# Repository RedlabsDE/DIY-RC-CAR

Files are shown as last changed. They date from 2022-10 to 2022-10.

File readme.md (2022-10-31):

# Create a simple DIY remote controlled car

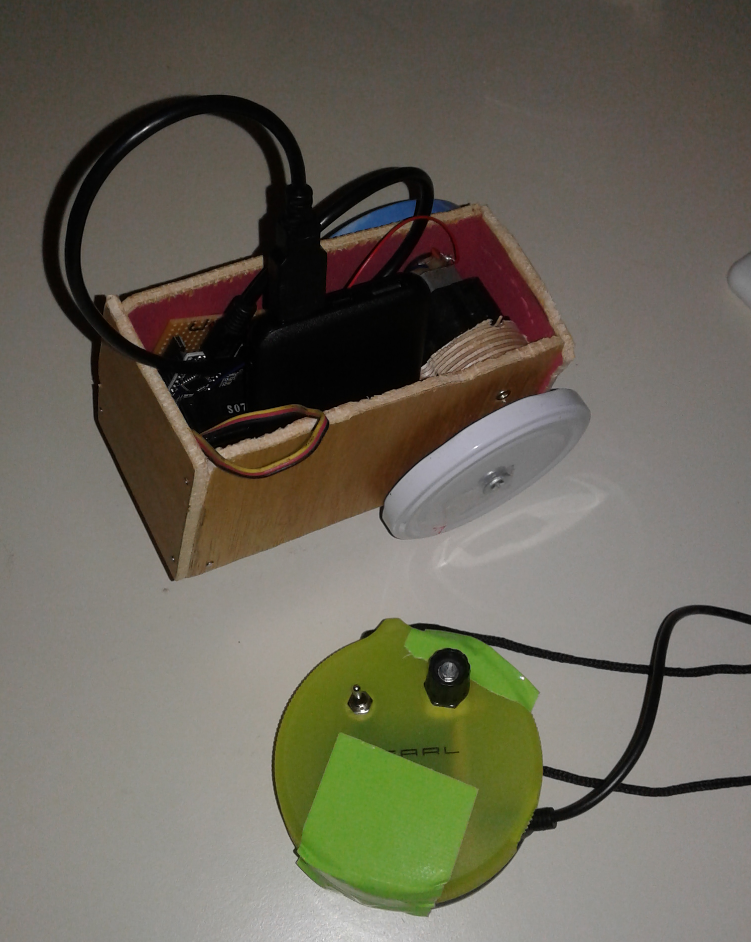
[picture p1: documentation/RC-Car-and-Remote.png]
Car and Remote


### What is this repository for? ###

* Quick summary  
	- RC and Car are bothed based on an arduino and will communicate via a wireless module (NRF24L01, 2.4GHz)
	- The RC (transmitter) looks for user input (Buttons,..) and send current state
	- The Car (receiver) reacts to received user input and set direction and speed of motor
	- Receiver and Transmitter are powered by a small USB Powerbank

## Firmware Setup ##
Too keep it simple, RC (transmitter) and the car (receiver) share the same arduino code.

- upload sketch to transmitter & receicer
```
#define TARGET_TRANSMITTER  1 //Remote Control
#define TARGET_RECEIVER     2 //Car

#define USED_TARGET TARGET_TRANSMITTER //<<< set target to be compiled
```
- check connection: if status LED flashes fast on receiver/transmitter there is no connection (motor stops if connection is lost)

## Hardware Setup ##

- Find schematics of transmitter and receiver in `...\RC-Transceiver\hardware\schematic`
- Find datasheets of used components in `...\RC-Transceiver\hardware\datasheet`

- `NRF24L01:` Transmitter and Receiver use same NRF pin setup. Find nice introduction here:  https://lastminuteengineers.com/nrf24l01-arduino-wireless-communication/

| Signal | Arduino Pin |
|---|---|
| NRF_MOSI 		| 11 |
| NRF_MISO | 12 	|
| NRF_MISO | 13 	|
| NRF_CE 	| 7 	|
| NRF_CSN 	| 8 	|
| NRF_IRQ 	| N/A 	|

### Transmitter ###
- `Board:` Arduino nano (with USB-mini connector)
- `Supply:` 5V (USB Powerbank) via Arduino USB connector
- `NRF24L01:` Connect NRF supply pin to 3V, Arduino Pro Mini: "VCC"
- `Push Buttons:` connect other pin to ground (active low)
- `Status LED:` connect other pin to ground (active high)
- `Potentiometer:` connect upper pin to VCC, lower pin to gnd, add capacitor to gnd on middle pin

| Signal 	| Arduino Pin |
|---		|---		|
| LED_STATUS		|10 		|
| Pushbutton_1 		|2 			|
| Pushbutton_2 		|3 			|
| Poti_1			|0 (A0)			|

### Receiver ###
- `Board:` Arduino nano (with USB-mini connector)
- `Supply:` 5V (USB Powerbank) via Arduino USB connector
- `NRF24L01:` Connect NRF supply pin to 3V, Arduino Nano: "3V3"
- `Status LED:` connect other pin to ground (active high)
- `Servo:` connect supply pin to 5V
- `Motor Driver:` connect supply pin to 5V *(H-Bridge IC could be replaced by 2xNFET + 2xPFET)*
- `DC Motor:` Connect Motor pins to motor driver

| Signal | Arduino Pin |
|---	|---		|
| LED_STATUS	|10 		|
| Servo1_Control|9 			|

| Signal 		| H-Bridge 	| Arduino Pin |
|---		|---	|---	|
| DCM1_GateP_neg	|G4			|3 			|
| DCM1_GateP_pos	|G1			|4 			|
| DCM1_GateN_neg	|G3			|5 (PWM) 		|
| DCM1_GateN_pos	|G2			|6 (PWM) 		|

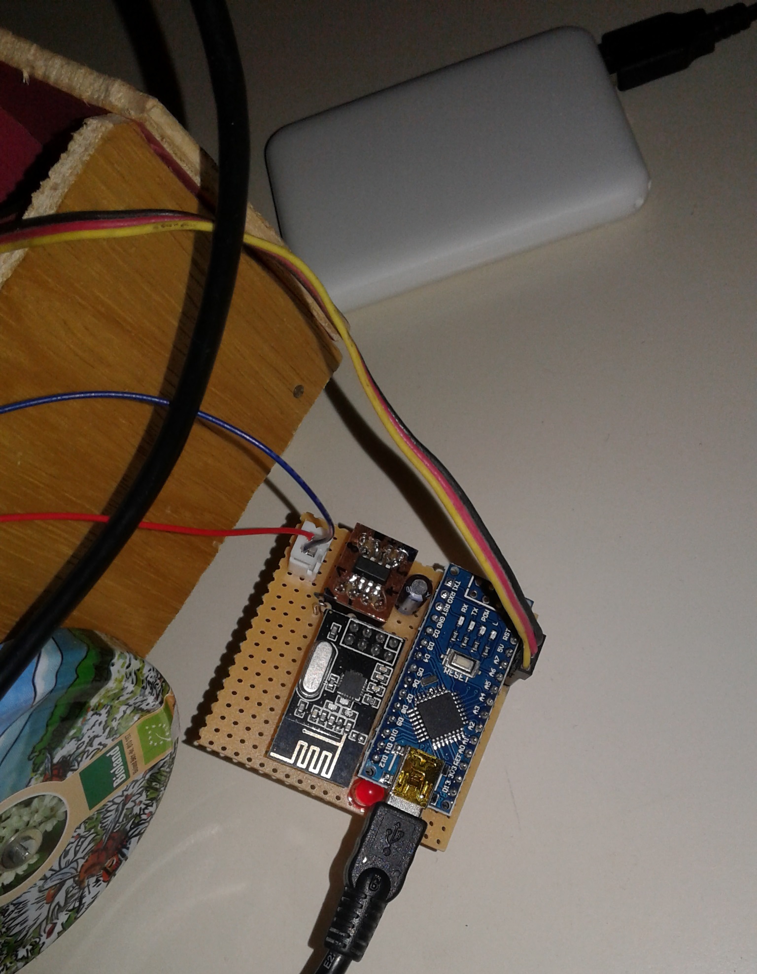
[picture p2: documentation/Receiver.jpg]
Receiver Circuit


## Mechanic Setup ##
### Transmitter ###
- A simple plastic box is used as RC housing
- Set direction of car: use potentiometer
- Move forward/backward: Use dual push switch (push&hold), idle position is stop

### Receiver ###
- As a car frame, wooden plates are nailed together (could be easily done by kids)
- As back wheels old metal caps are screwed to the axis (axis made of threaded standoff)
- Drive car forward and backward: Use single DC Motor to drive both back wheels (old DC motor with gears)
- Set direction of car: Use Servo to set angle of single front wheel (wheel is glued to the servo)

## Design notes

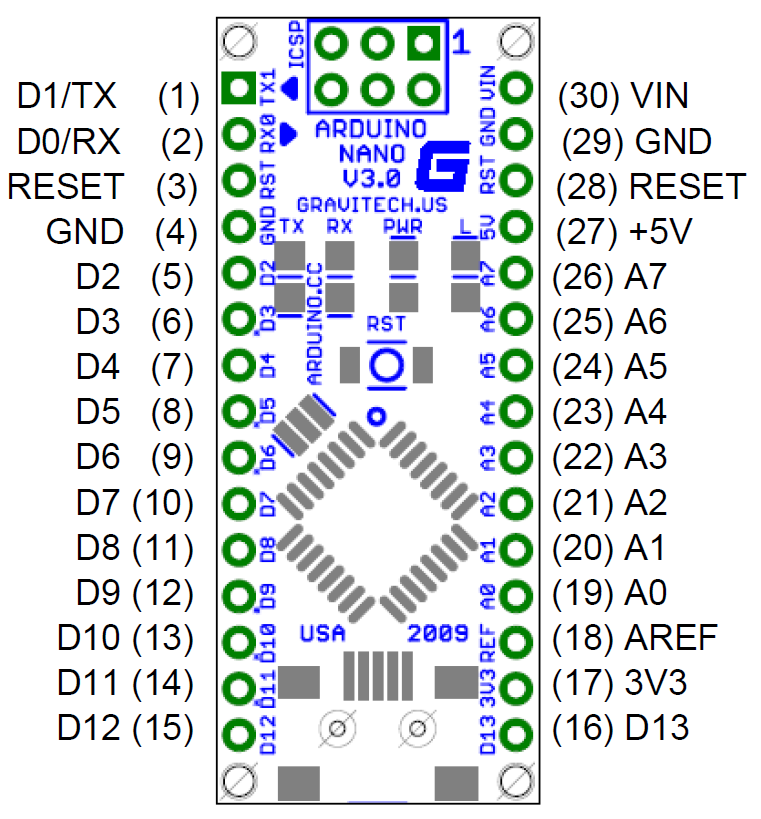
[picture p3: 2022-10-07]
hardware/datasheet/Arduino_Nano_Pinout.png

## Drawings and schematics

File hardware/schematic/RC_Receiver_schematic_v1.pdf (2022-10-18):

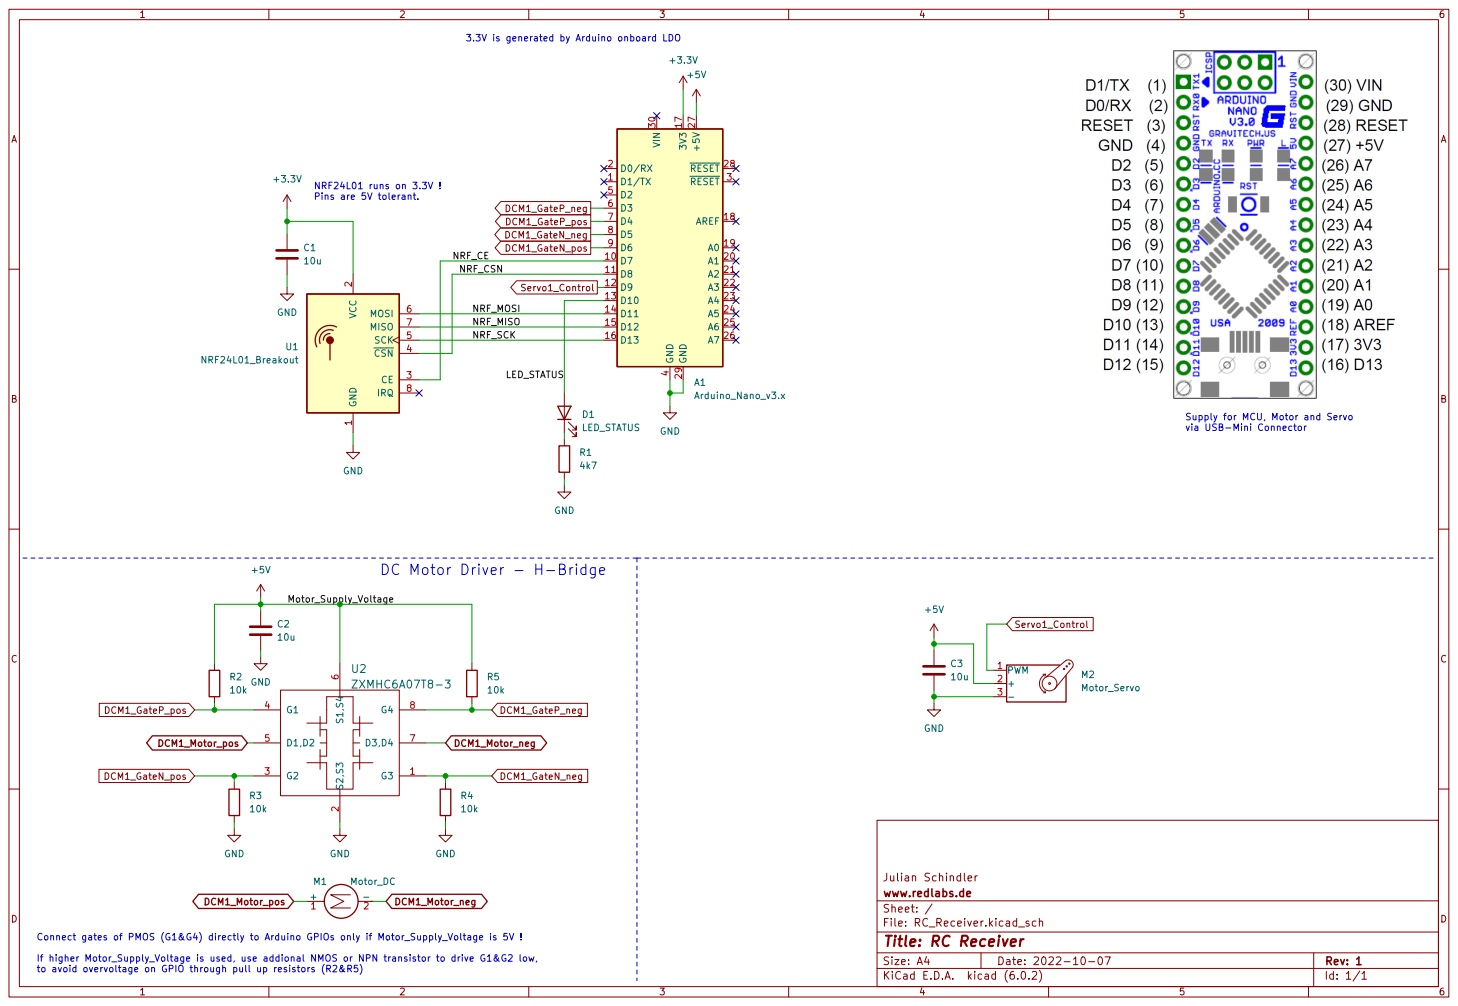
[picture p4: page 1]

2 CE 3 ~{CSN} 4 SCK 5 MOSI 6 MISO 7

Supply for MCU, Motor and Servo

DC Motor Driver - H-Bridge

File: RC_Receiver.kicad_sch Sheet: / www.redlabs.de

Connect gates of PMOS (G1&G4) directly to Arduino GPIOs only if Motor_Supply_Voltage is 5V !

Id: 1/1 Title: RC Receiver

If higher Motor_Supply_Voltage is used, use addional NMOS or NPN transistor to drive G1&G2 low,
to avoid overvoltage on GPIO through pull up resistors (R2&R5)

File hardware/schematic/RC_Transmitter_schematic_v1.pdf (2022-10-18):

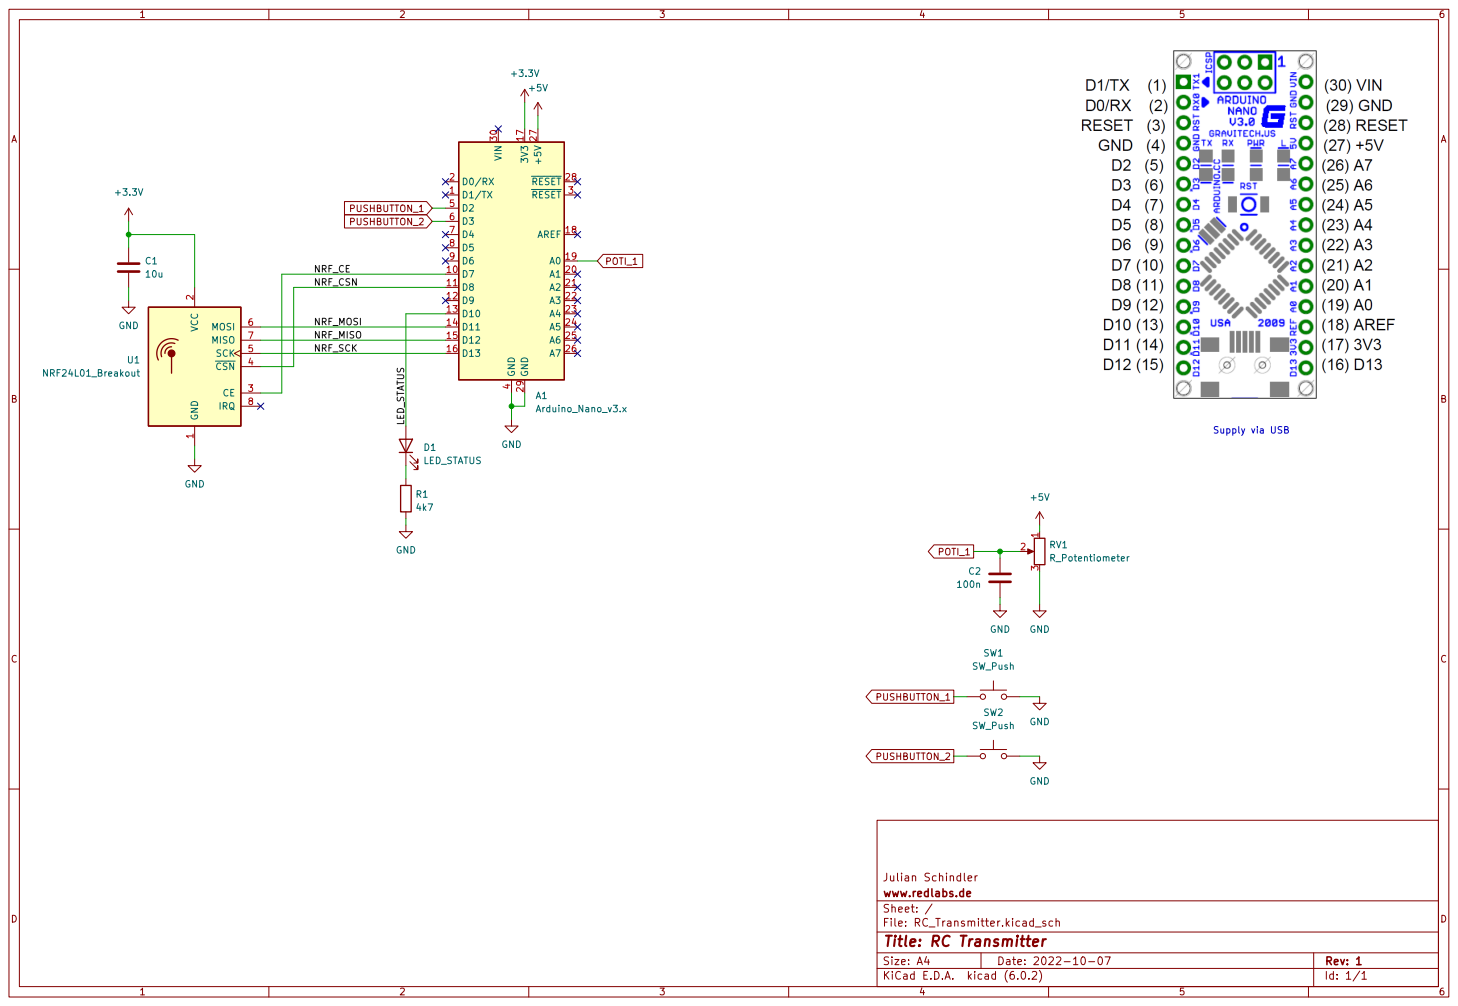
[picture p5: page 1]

2 CE 3 ~{CSN} 4 SCK 5 MOSI 6 MISO 7

File: RC_Transmitter.kicad_sch Sheet: / www.redlabs.de

Id: 1/1 Title: RC Transmitter

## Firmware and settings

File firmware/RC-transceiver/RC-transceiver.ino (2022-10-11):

//////////////////////////////////////////////////////////////////////////////
///
/// \file       RC-transceiver
/// \brief      Remote Control Transmitter and Receiver
/// \author     Julian Schindler
/// \date       21.09.2022
/// \version    1.0
/// \par        Editor
///             Arduino IDE
/// \par        Board
///             Arduino Pro or Pro Mini
/// \par        Prozessor
///             ATMega328
/// \par        COM Port Setting (debug)
///             Baud: 115200 / 8N1
///
/// \par        Organization
///             redlabs.de
/// \par        Repository
///             https://github.com/Julian-Schindler/RC-Transceiver
//////////////////////////////////////////////////////////////////////////////
//////////////////////////////////////////////////////////////////////////////
#define TARGET_TRANSMITTER  1 //Remote Control
#define TARGET_RECEIVER     2 //Car

#define USED_TARGET TARGET_RECEIVER   //<<<<<<<<<<<<<<<<<<<<<<<<<<<<<<<<<< select mode to download to your arduino

//////////////////////////////////////////////////////////////////////////////
//defines to customize the system
#define DEBUG true //used for debug serial output

#define DEBUG_SERIAL_PRINT_RADIO_COMMUNICATION true //serial print everything that is sent or received via radio
#define DEBUG_SKIP_RADIO_COMMUNICATION false //use for test-setup without working radio communication

#define USE_BATTERY_MONITOR false //if system is powered by a battery the monitor will shutdown the system (transmitter) if battery voltage is below BATTERY_MIN_MV
//////////////////////////////////////////////////////////////////////////////

enum STATUS_LED
{
  SL_OFF,
  SL_ON,
  SL_BLINK_FAST,
  SL_BLINK_SLOW,
};
//////////////////////////////////////////////////////////////////////////////

#ifdef __AVR__
  #include <avr/power.h>
#endif

#include <avr/sleep.h>

#include <SPI.h>
#include "nRF24L01.h"
#include "RF24.h"
#include "printf.h"

#define PIN_NRF_CE  7 //<<< custom setting default
#define PIN_NRF_CSN 8 //<<< custom setting default
/* Hardware configuration: Set up nRF24L01 radio on SPI bus plus pins 7 & 8 */
RF24 radio(PIN_NRF_CE,PIN_NRF_CSN);
const uint64_t pipes[2] = { 0xABCDABCD71LL, 0x544d52687CLL };              // Radio pipe addresses for the 2 nodes to communicate.

#include <Servo.h>
Servo myservo1;  //use this servo to set direcetion (angle of front wheel)

#include "dc_motor.h"
DC_MOTOR main_engine(20,255,5); //use this motor as main engine to drive forward/backward

#include "rc_hmi.h" //user interface (buttons, ...)
#include "rc_message_types.h"
#include "rc-transceiver.h"



//////////////////////////////////////////////////////////////////////////////
void setup() 
{
  Serial.begin(115200);
  Serial.println("Redlabs - RC Tranceiver Project");


  //rx/tx specific setup
  #if(USED_TARGET == TARGET_TRANSMITTER)
    Serial.println("Start transmitter mode");
    init_hmi_data();
    setup_transmitter();
  #else if( USED_TARGET == TARGET_RECEIVER)
    Serial.println("Start receiver mode");
    setup_receiver();
  #endif

#if(DEBUG_SKIP_RADIO_COMMUNICATION == false)
  //common setup
  radio.begin();
  radio.setAutoAck(1);                    // Ensure autoACK is enabled
  //radio.enableAckPayload();               // Allow optional ack payloads
  radio.setRetries(0, 15);                // Smallest time between retries, max no. of retries
  radio.setPayloadSize(RC_COMMAND_PAYLOAD_SIZE);                // Here we are sending 1-byte payloads to test the call-response speed
  radio.openWritingPipe(pipes[0]);        // Both radios listen on the same pipes by default, and switch when writing
  radio.openReadingPipe(1, pipes[0]);
  
  radio.startListening();                 // Start listening
  //radio.printDetails();                   // Dump the configuration of the rf unit for debugging
  Serial.println(" rx started");
#endif

  //rx/tx specific setup
  #if(USED_TARGET == TARGET_TRANSMITTER)
    rc_send_command_type(COMMAND_TYPE_STARTUP);
  #else if( USED_TARGET == TARGET_RECEIVER)
    //rc_send_command_type(COMMAND_TYPE_STARTUP);
  #endif
  
}

void setup_transmitter()
{
  //check battery voltage
  if(battery_voltage_ok())
  {
    //procceed if it is in range ...
    system_init_transmitter();  
  }
  else
  {  
    //go to sleep forever, start again only by (power-)reset
    system_shutdown_transmitter();
  }
}
void setup_receiver()
{
  system_init_receiver();

  myservo1.attach(PIN_SERVO_1);  // attaches the servo on pin x to the servo object
  

  myservo1.write(180/2 - 50); //move to left  
  myservo1.write(180/2 + 50); //move to right   
  myservo1.write(180/2); //move to mid position  

  main_engine.init_h_bridge(3,4,5,6,LOW);
  main_engine.set_speed(100); //set fixed speed, used for both directions
  main_engine.set_direction(DC_MOTOR::DCM_STOP);
  main_engine.set_enable(true);
}

////////////////////////////////////////////////////////////////////////////////////////////////////////////////////////////////////////////////////////////
void loop() 
{
  // put your main code here, to run repeatedly:
  #if(USED_TARGET == TARGET_TRANSMITTER)
    loop_transmitter();
  #else if( USED_TARGET == TARGET_RECEIVER)
    loop_receiver();
  #endif
}

int loopCounter = 0;
//////////////////////////////////////////////////////////////////////////////
void loop_transmitter()
{  
  static bool last_tx_success = false;
  static int last_tx_timeout = 0;
  last_tx_timeout++;

  //TODO: system_check_transmitter(); //check battery and powerbutton state, if needed
  
  //check if HMI data changed
  if(hmi_has_changed())
  {
    //send out last_hmi_data via radio
    last_tx_success = rc_send_command_type(COMMAND_TYPE_DATA_HMI);
    last_tx_timeout = 0;
  }
  else if(last_tx_timeout > LOOP_MS_TO_COUNT(3000))
  {
    last_tx_success = rc_send_command_type(COMMAND_TYPE_PING);
    last_tx_timeout = 0;
  }

  indicate_status_led(last_tx_success==true ? SL_BLINK_SLOW : SL_BLINK_FAST); //last data received within timout: blink fast, timeout expired: blink slow

  loopCounter++;  
  //GO_TO_SLEEP(true); //sleep some time to save energy
  _delay_ms(10); //dummy
}
//////////////////////////////////////////////////////////////////////////////




void loop_receiver()
{
  static bool connected = false;
  static int last_rx_timeout = 0;
  
  if(last_rx_timeout<LOOP_MS_TO_COUNT(5000))
  {
    last_rx_timeout++;
  }
  else
  {
    connected = false; //5 seconds without receiving any data
    receiver_connection_lost();
  }

  if( radio.available())
  {
    struct RC_COMMAND rc_command_received;
    struct RC_COMMAND* p_command = &rc_command_received;

    radio.read(p_command, sizeof(*p_command));

    Serial.println();
    Serial.print(" RX RC_COMMAND: ");    
    printStruct(((uint8_t*)p_command),  sizeof(*p_command));

    if(rc_handle_received_data(p_command))
    {
      //if packet is valid, reset rx timeout
      last_rx_timeout = 0;
      connected = true;
    }  
  }

  main_engine.process();

  indicate_status_led(connected==true ? SL_BLINK_SLOW : SL_BLINK_FAST); //last data received within timout: blink fast, timeout expired: blink slow

  loopCounter++;
  //GO_TO_SLEEP(true); //sleep some time to save energy
  _delay_ms(10); //dummy
}

void receiver_connection_lost()
{
  main_engine.set_direction(DC_MOTOR::DCM_STOP);
  //indication of connection loss in loop
}



void indicate_status_led(uint8_t status)
{
  int blink_time = 0;

  switch(status)
  {
    case SL_OFF:
      digitalWrite(PIN_LED_STATUS, LOW);
    break;
    case SL_ON:
      digitalWrite(PIN_LED_STATUS, HIGH);
    break;
    case SL_BLINK_FAST:
      blink_time = LOOP_MS_TO_COUNT(100);
    break;
    case SL_BLINK_SLOW:
      blink_time = LOOP_MS_TO_COUNT(1000);
    break;
    default:
    break;
  }

  if( (blink_time!=0) && (loopCounter % blink_time == 0))
  {
    digitalWrite(PIN_LED_STATUS, !digitalRead(PIN_LED_STATUS));
  }  
}

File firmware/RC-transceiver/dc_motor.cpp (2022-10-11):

#include "dc_motor.h"

DC_MOTOR::DC_MOTOR()
{
    speed_min = 5;
    speed_max = 255;
    speed_increment = 2;

    reset();
}

DC_MOTOR::DC_MOTOR(uint8_t speedMin, uint8_t speedMax, uint8_t speedIncrement)
{
    speed_min = speedMin;
    speed_max = speedMax;
    speed_increment = speedIncrement;

    reset();
}

void DC_MOTOR::reset()
{
    speed_current = 0;
    direction_current = DCM_STOP;

    speed_destination = 0;
    direction_destination = DCM_STOP;

    enable = false;
    initDone = false;
}

//for use of HBridge "ZXMHC6A07T8" use init_h_bridge(G4, G1, G3, G2)
void DC_MOTOR::init_h_bridge(int pinNum_gateP_neg, int pinNum_gateP_pos, int pinNum_gateN_neg, int pinNum_gateN_pos, bool pmos_active_state)
{
    pin_gateP_neg = pinNum_gateP_neg;
    pin_gateP_pos = pinNum_gateP_pos;
    pin_gateN_neg = pinNum_gateN_neg;
    pin_gateN_pos = pinNum_gateN_pos;

    pmos_active = pmos_active_state;
    bool PMOS_INACTIVE = pmos_active;

    pinMode(pin_gateP_neg, OUTPUT);
    pinMode(pin_gateP_pos, OUTPUT);
    pinMode(pin_gateN_pos, OUTPUT); //PWM
    pinMode(pin_gateN_neg, OUTPUT); //PWM

    digitalWrite(pin_gateP_neg, PMOS_INACTIVE);
    digitalWrite(pin_gateP_pos, PMOS_INACTIVE);
    digitalWrite(pin_gateN_pos, LOW);
    digitalWrite(pin_gateN_neg, LOW);

    usedDriverType = DRIVER_HBRIGE;
    initDone = true;
}

//not tested
void DC_MOTOR::init_L9110(int pinNum_dir, int pinNum_pwm)
{
    pin_dir = pinNum_dir;
    pin_pwm = pinNum_pwm;

    pinMode(pin_dir, OUTPUT);
    pinMode(pin_pwm, OUTPUT); //PWM

    digitalWrite(pin_dir, LOW);
    digitalWrite(pin_pwm, LOW);

    usedDriverType = DRIVER_L9110;
    initDone = true;
}

void DC_MOTOR::set_enable(bool motorEnable)
{
    enable = motorEnable;
}

void DC_MOTOR::set_direction(enum DC_MOTOR_DIRECTION dir)
{
  direction_destination = dir;
}

void DC_MOTOR::set_speed(uint8_t speed)
{
  //TODO add minimum speed (absolut min is step size in motor ramp up/down)
  if(speed < speed_min)
  {
    speed = speed_min;
  }
  else if (speed > speed_max)
  {
    speed = speed_max;
  }
  speed_destination = speed;
}

//set motor speed / direction. Return false if motor driver is not initialized.
bool DC_MOTOR::process()
{
    if(direction_current != direction_destination) //ramp speed to 0, change direction, ramp speed up
    {
        //change of direction from FWD or RWD
        if((direction_current==DCM_FWD)||(direction_current==DCM_RWD))
        {
            speed_current -= speed_increment; //ramp down speed
            #if DEBUG
            Serial.print("x");
            #endif

            if(speed_current <= speed_min) //if speed is low enough to stop, change direction
            {
                direction_current = direction_destination;
                #if DEBUG
                Serial.print("c");
                #endif
            }

        }
        else //change from stop to other direction
        {
            direction_current = direction_destination;
        }
    }
    else if(speed_current != speed_destination) //change in motor speed, without change of direction
    {
        if(speed_current > speed_destination) //if actual speed is higher than new speed
        {
            speed_current -= speed_increment; //ramp down speed

            #if DEBUG
            Serial.print("<");
            #endif
        }
        else if(speed_current < speed_destination) //if actual speed is lower than new speed
        {
            speed_current += speed_increment; //ramp up speed
            #if DEBUG
            Serial.print(">");
            #endif
        }
    }
    else //no change
    {
        speed_current = speed_destination; //just set speed again
    }

    //limit speed
    if(speed_current > speed_max)
    {
        speed_current = speed_max;
    }
    else if(speed_current< speed_min)
    {
        speed_current = speed_min;
    }

    if(enable == false)
    {
        speed_current = 0;
        direction_current = DCM_STOP;
        #if DEBUG
        Serial.println("enable=false");
        #endif
    }
    if(initDone == false)
    {
        #if DEBUG
        Serial.println("initDone=false");
        #endif
        return false;
    }

    if(usedDriverType == DRIVER_HBRIGE)
    {
        process_h_bridge();
    }
    else if(usedDriverType == DRIVER_L9110)
    {
        process_L9110();
    }

    return true;
}



//output speed and direction to H-Bridge (use two GPIOs and two PWMs)
void DC_MOTOR::process_h_bridge()
{
    //here, the P-MOSFETs are driven directly by a GPIO (pin low = active). If inverting transistors are used (if V_motor > V_uC), switch following settings.
    bool PMOS_ACTIVE = pmos_active;
    bool PMOS_INACTIVE = !pmos_active;

    if(direction_current == DCM_FWD)
    {
      digitalWrite(pin_gateP_pos, PMOS_ACTIVE); //G1, set Motor-Pos to supply voltage
      digitalWrite(pin_gateP_neg, PMOS_INACTIVE); //G4, disconnect Motor-Neg from supply voltage
      analogWrite(pin_gateN_neg,speed_current); //G3, PWM output to low-side switch on Motor-Neg
      analogWrite(pin_gateN_pos,0); //G2, stop PWM output to low-side switch on Motor-Pos
    }
    else if (direction_current == DCM_RWD)
    {
      digitalWrite(pin_gateP_neg, PMOS_ACTIVE); //G4, set Motor-Neg to supply voltage
      digitalWrite(pin_gateP_pos, PMOS_INACTIVE); //G1, disconnect Motor-Pos from supply voltage
      analogWrite(pin_gateN_pos,speed_current); //G2, PWM output to low-side switch on Motor-Pos
      analogWrite(pin_gateN_neg,0); //G3, stop PWM output to low-side switch on Motor-Neg
    }
    else //motor stopped
    {
      digitalWrite(pin_gateP_pos, PMOS_INACTIVE); //G1, disconnect Motor-Pos from supply voltage
      digitalWrite(pin_gateP_neg, PMOS_INACTIVE); //G4, disconnect Motor-Neg from supply voltage
      analogWrite(pin_gateN_neg,0); //G3, stop PWM output to low-side switch on Motor-Neg
      analogWrite(pin_gateN_pos,0); //G2, stop PWM output to low-side switch on Motor-Pos
    }
}

//not tested
void DC_MOTOR::process_L9110()
{
  //output speed and direction to motor driver (use one dirction GPIO and one for PWM)
    if(direction_current == DCM_FWD)
    {
      digitalWrite(pin_dir, LOW);
      analogWrite(pin_pwm,speed_current); //PWM output to motor driver
    }
    else if (direction_current == DCM_RWD)
    {
      digitalWrite(pin_dir, HIGH);
      analogWrite(pin_pwm,255-speed_current); //PWM inverse output to motor driver
    }
    else
    {
      digitalWrite(pin_dir, LOW);
      analogWrite(pin_pwm,0); //PWM output to motor driver
    }
}

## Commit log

2022-09-21 start with arduino code
    add basic structure
2022-09-22 add pin defines for first test on hardware
2022-09-23 add basic servo control to receiver
2022-09-23 add battery measurement, add system shutdown
2022-09-23 add function to get averaged adc measurement
2022-09-23 add servo control
2022-09-26 add dc motor control
2022-09-26 add motor pin defs
2022-09-27 add dc motor control struct
2022-10-06 add dc motor control via hmi buttons, add status led
2022-10-06 first test with dc motor. Works nice
2022-10-07 add kicad schematic
    [RC_Receiver.kicad_pcb, RC_Receiver.kicad_sch, RC_Transmitter.kicad_pcb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]
2022-10-07 add schematic net names like described in the readme
    [RC_Receiver.kicad_sch, RC_Transmitter.kicad_sch]
2022-10-10 connect HMI (Button & Poti) to MCU
    [RC_Transmitter.kicad_sch]
2022-10-10 add motor driver H-bridge
    [RC_Receiver.kicad_sch]
2022-10-11 * add h-bridge driver
    [RC_Receiver.kicad_sch]
2022-10-11 * replace motor control by new class DC_MOTOR
    [RC-transceiver.ino, dc_motor.cpp, rc-transceiver.h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]
2022-10-11 * correct handle rx timeout
    [RC-transceiver.ino, rc-transceiver.h]
2022-10-13 limit servo range
2022-10-14 change value of series resistor for status LED
    [RC_Receiver.kicad_sch, RC_Transmitter.kicad_sch]
2022-10-18 * add datasheets and schematics
